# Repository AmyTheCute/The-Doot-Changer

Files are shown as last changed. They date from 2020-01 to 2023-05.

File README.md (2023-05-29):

# The-Doot-Changer

**Warning, project is abandonded for the time being, potential Doot Eternal might be in progress down the line, for the time being, feel free to email me at Amythemaplebun@gmail.com to ask for guidance/files to fit this project into your own printers, or simply ask for what I learned making this tool changer**

Files and designs for The Doot Changer
Welcome to the official page for the Doot Changer Project! Keep in mind that Doot Changer Twist is still in alpha and although this version is working well you should build it at risk

Update: this project is seriously out of date.
But I'm planning on leaving the country for education. I'm designing a far superior version. expect fast printing speeds, a more awesome mechanism when i finally arrive!
However, aside from the motion system you should feel free to transfer the locking mechanism to your printer, however if you're in a hurry you can Message me to design you the new locking mechanism, or you can simply upgrade when i'm done as it barely costs anything to upgreade (it needs aluminium tape and yup, that's it. add 2 wires to your carriage and leave it there for the upgrade

**WARNING**: Doot Changer Twist is missing some files. Contact me at Twitter: https://twitter.com/AmyTheBun to get the files, they're unoptimized and therefore not published. They'll be re-designed and published very soon

Doot Changer Mag Is well tested with bowden tools.

The Doot Changer project is aiming to bring tool changing to the average hobbyists to encourage creative tool design and so on. The Doot Changer Mag is well tested with bowden tools and slightly tested with directdrive tools.

Doot Changer Mag barely costs 20$ in BOM and can be added very easily to any existing printer that moves the hotend in both the X and Y axis. the assembly is very easily and the Y Axis space reducion is dependant on the printer. Expect 50-100mm of y axis loss.
Doot Changer Mag is also self aligning and generally more trouble free, upon crashes the tool is more likely to just fall and if the docks aren't aligned it'll pick itself up. Subtractive tools aren't tested yet. Only bowden tools are tested extensively and directdrive tools are only simulated by attaching weights to the bowden tools (300g) at 1200 accel
The Doot Changer Mag motion system is HIGHLY RECOMMENDED if you're using a HEVO for a faster printing speed and higher print quality. Currently you'd need to design your Own cariage to make it work with Mag but it should be very easy.

Doot Changer Twist is an entire 3DPrinter that costs 600-800$ depending on your config with 2 tools. the "Sweet spot" config costs 750$ on aliexpress with 2 trianglelab BMG + V6 tools, Robodigg Rails and a tooling plate + a 220v AC heated bed.
Doot Changer Twist uses a Motor (Right now, 28-BYJ-48, Soon it'll switch to a no-name toy DC motor) to lock the tools. therefore to unlock the tools you'd have to break the plastic components. This tool changer changer is far less forgiving to mistakes but has a stronger lock.
The docks for this tool changer also take less space but there are more compact docks potentially in work for the Doot Changer Mag. This printer mainly uses dowel pins and you can use Acetal filament for the wedge.
This printer is also a 150$ upgraede (1 additional trinaglelab tools with extruders) for any existing HEVO and reduces anywhere from 80-100mm of Y Axis usable print volume due to the tools taking space. if building a Doot Changer from scratch simply increase the Y axis by 100-110mm and the x axis by 10-20mm (to make space for potential endstop auto nozzle calibrations and accessories) The rods should remain the same size as well as the X axis rails, However a rod holder will need to be designed (ask me for help!)

This project took a year and made my skin bleed, took all my time and cost me more than 1500$ of prototype and researching. I put my heart into this project and chose to use easily sourcable materials so everyone can enjoy what I enjoy.
Please consider donating to this open source project with Crypto Currency or gift cards, I live in Iran so there are no other options for donations sadly. I'm HOPEFULLY moving to canada by next year. I plan to design a far better printer there if I get free time!
Do message me if you decide to donate so I can squeak out loud very hard ;3 (never made a penny before!)

Update!: Thanks to awesome Anya (https://twitter.com/_Iyalei?s=09) for being the first doot changer donator ^~^ bunny heart is truly molten and warm enough to print PEEK

ToDo: Youtube guide

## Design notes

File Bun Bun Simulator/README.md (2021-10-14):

This is a per tool pebble wiper that has the BOM fo only a spring

EDIT: WARNING! this design stopped working, no idea why but the pebbles stick so hard to the kapton tape now that even with my nails it takes a lot of effort to push it, so it needs powerful springs (3x the same spring I use, which is troublesome because my fan duct is what's pushing it and it's not very strongly mounted)

i'm working on 4 new designs that hopefully might work, so in the meantime, try this at your own risk! tho i gotta admit abs works perfect with this, but PLA specially sticks SUPER well, to the point of it not being able to be poked off without help. and the slope at the end of the block sometimes makes the not fully cooled filament deform and get under the block's rail, anyways I have a few ideas on how to fix it! but i'm very sick

If you plan on modifying this to fit another printer, know that some tilt/flex is a good thing if you plant to use the wiping moving block (Block.stl) as a brush to hit the tip of the nozzle too as it has chamfers to rub on the nozzles and some flex helps. however this isn't necessary and you can always add a silicone brush at the end

The extension spring I used:
Length without hooks: 25mm
inside diameter: 5mm
Material: carbon steel?
Image:

That's all I could find, you could also find something slightly weaker and  put it on both sides to insure that the pellets won't hit the spring? I haven't had issues so far tho.
the springs need to stretch 13-14mm and be left a bit stretched still in their "relaxed" poisition. so in total they need 15-18mm~ of travel

To assemble, Put lubrication compatible with your Block.stl (expect for any Nylon/acetal which doesn't need it) on all faces the block moves on expect the top one.
Put Kapton tape on where the pebble will be purged with some aluminium foil/tape under.
Put aluminium foil where the pellet/nozzle would touch to reduce the chance of adhesion.

here's mine:



Here's an older version in action!:
https://twitter.com/AmyTheBun/status/1445347870236946432?s=20

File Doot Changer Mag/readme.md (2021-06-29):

This is the Github page for The Doot Changer

Here are some footage and images and videos:
https://photos.app.goo.gl/33gT6J51nGpFnPVe7

This is printer mostly a modified HEVO but the actual tool changer is super modular and works with anything that moves the toolhead in both X and Y. A ton of credit goes to scott3d tech2c and other people I mentioned in the thingiverse page! Thank you all lovely people!

It's based of my HEVO. The stock build is MOSTLY for bowden but will work for direct drives potentially (limited testing). to make it work with dremels or heavier tools use the small circular hole for an additional magnet (it's only an indicator of where to put it, make it larger and use a ring magnet. keep in mind that if you want to add this YOU MUST NOT LET THE TWO MIDDLE MAGNETS TOUCH each other, put atleast 0.2mm or more space between the two, don't make it way too far tho. Magnets lose strengh quickly when too far apart)

my doot changer 2.0 is in the works, it's going well. I probably will at least ad the motion system as an addon here, it's much better than the stock one. plus it frees up the space lost to the docks

feel free to message me at https://twitter.com/AmyTheBun to ask anything

Donations (bitcoin only cause I live in Iran :( ):

Bitcoin wallet: bc1qhk2vj8rvw50vd60455dnn2gya4cqduanyrnwg3

for lightning network donations contact me at amythechloe@gmail.com since the links expire

XRP (Ripple): rGJVbxGnUKjaEziDkd7TMDE6gjxK1qMbLc

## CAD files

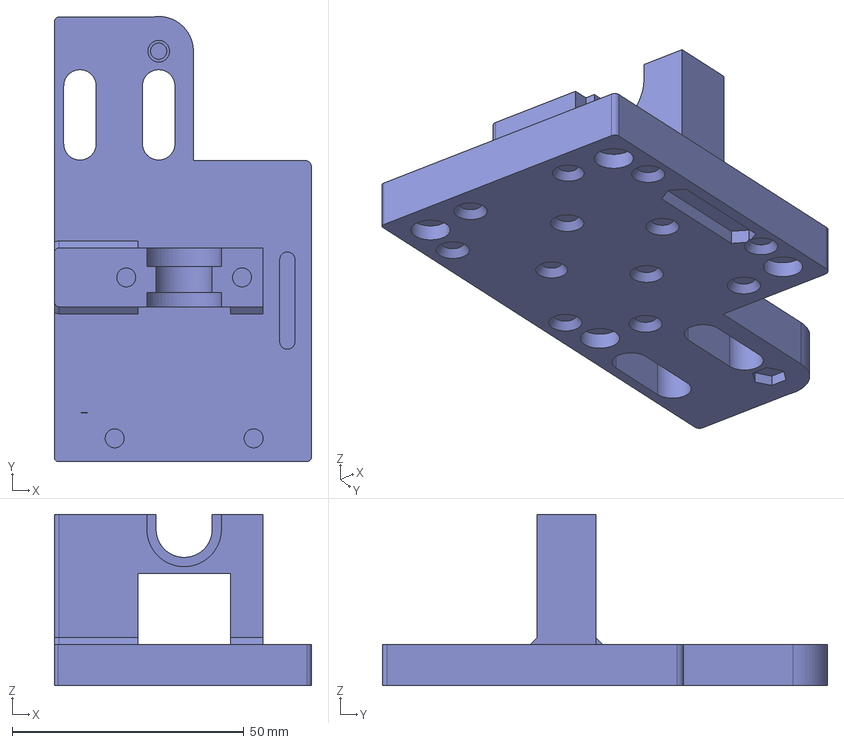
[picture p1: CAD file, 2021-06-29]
Doot Changer Mag/Carriage/Hotend assembly Tool Changer Included.iges
55.5 x 96.1 x 37.0 mm

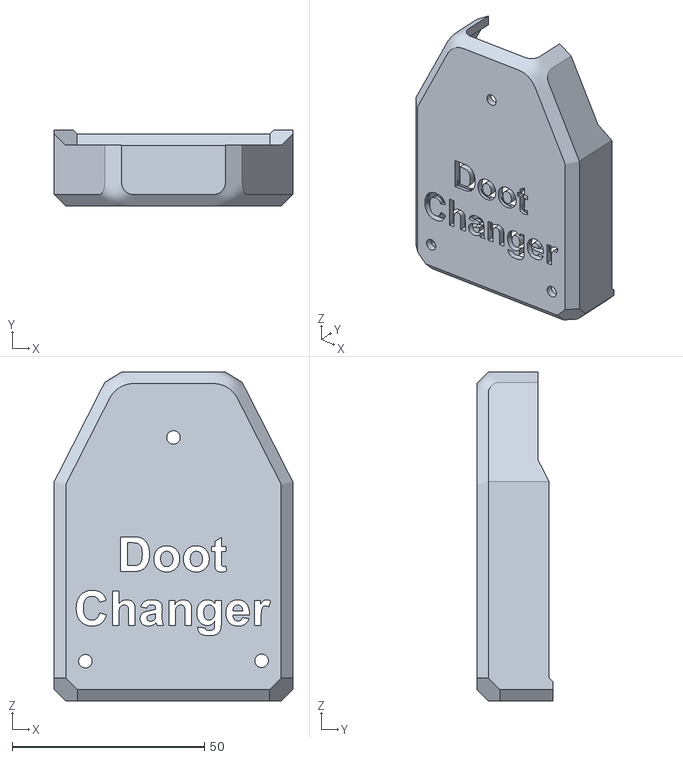
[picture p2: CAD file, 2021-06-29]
Doot Changer Twist/STL/Doot Changing Reward/Main.stl
62.0 x 19.8 x 85.5

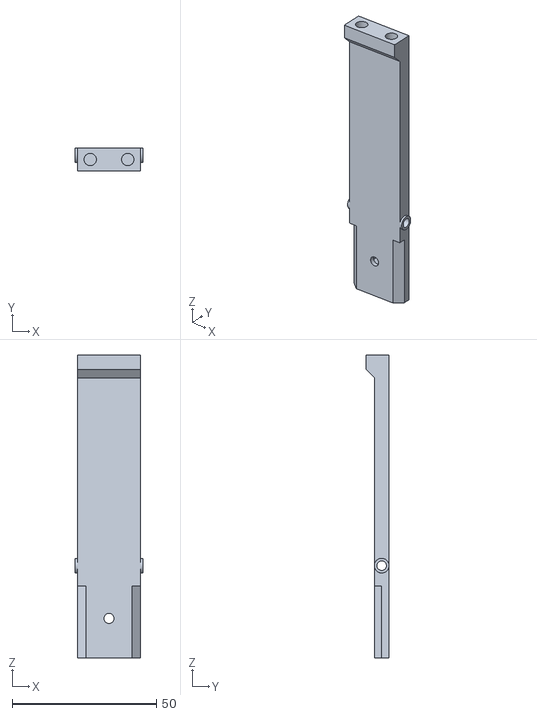
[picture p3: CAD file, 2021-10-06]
Bun Bun Simulator/Arm_Main.stl
23.6 x 8.00 x 105.0

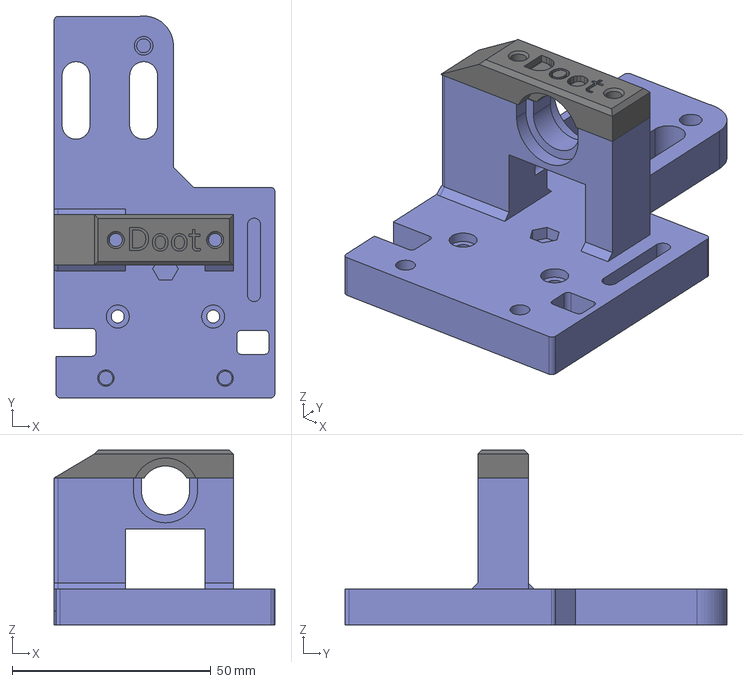
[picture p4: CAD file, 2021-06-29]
Doot Changer Mag/Carriage/Hotend assembly v10.iges
55.5 x 96.1 x 44.0 mm

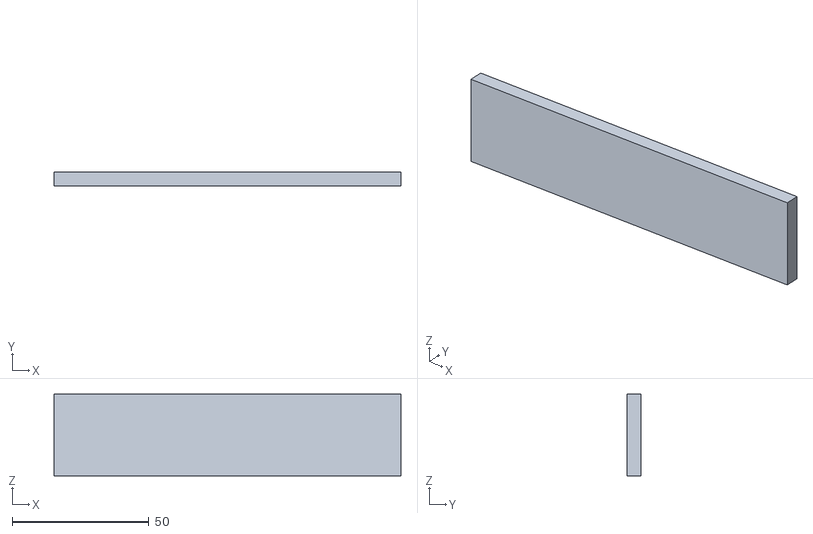
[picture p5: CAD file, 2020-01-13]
Doot Changer Mag/Logo/main.stl
127.0 x 5.00 x 30.0

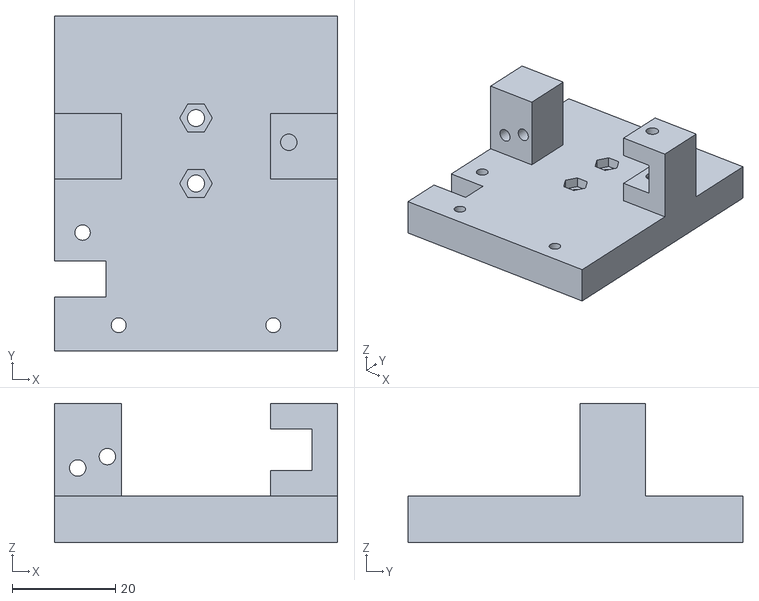
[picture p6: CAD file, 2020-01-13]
Doot Changer Mag/Depricated/Nozzle probe/actually main caswe.stl
55.0 x 65.0 x 27.0

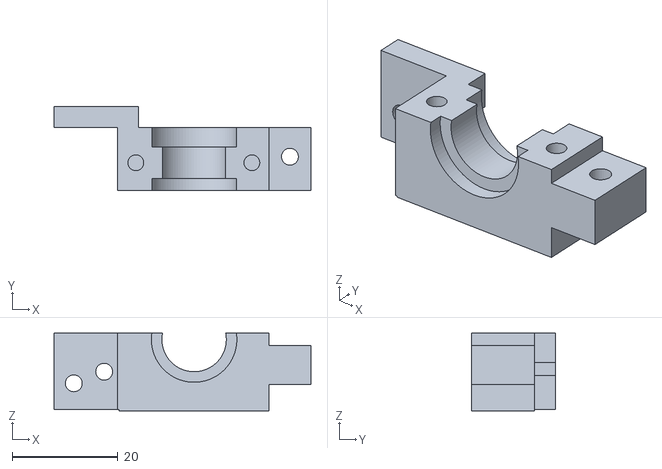
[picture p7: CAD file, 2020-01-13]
Doot Changer Mag/Depricated/Nozzle probe/main case.stl
48.7 x 16.0 x 14.7

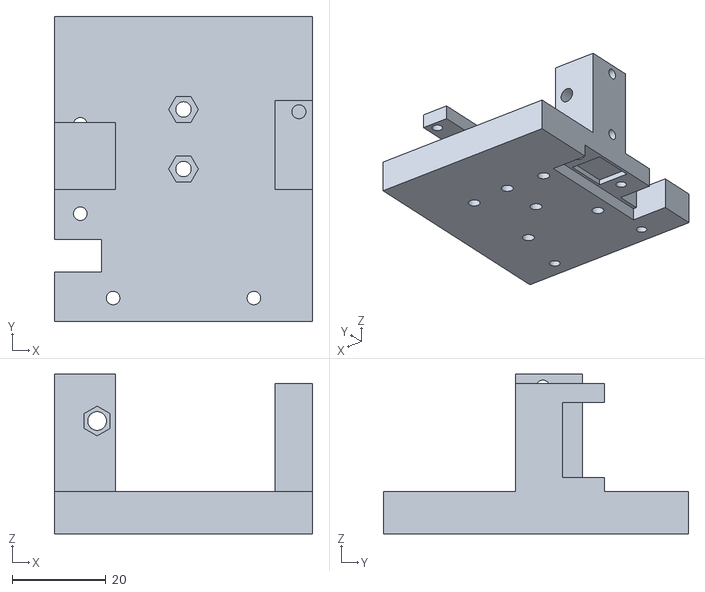
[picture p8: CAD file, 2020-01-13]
Doot Changer Mag/Depricated/Nozzle probe/hotend assembly.stl
55.0 x 65.0 x 34.0

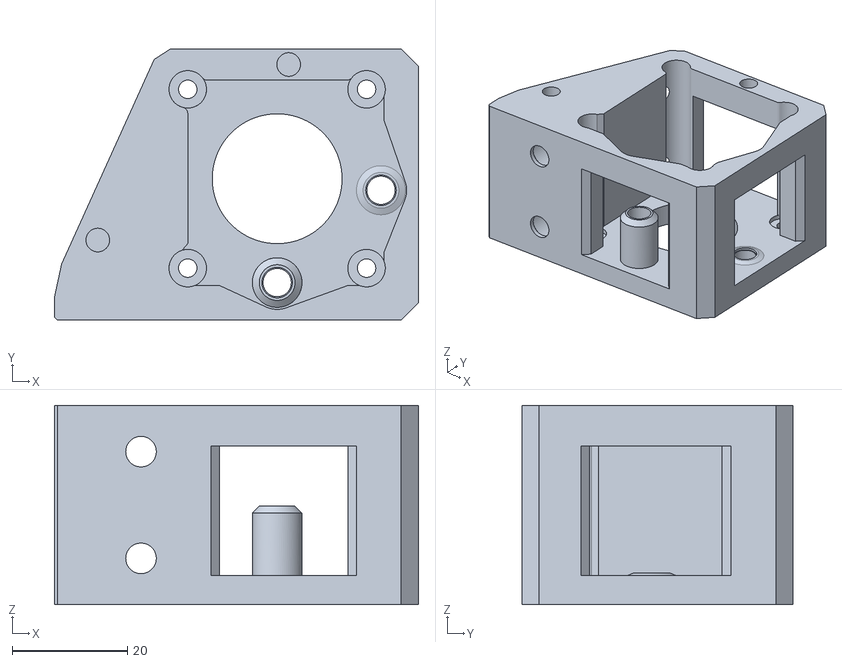
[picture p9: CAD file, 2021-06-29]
Doot Changer Twist/STL/Left_Motor_Main.stl
63.1 x 47.0 x 34.5

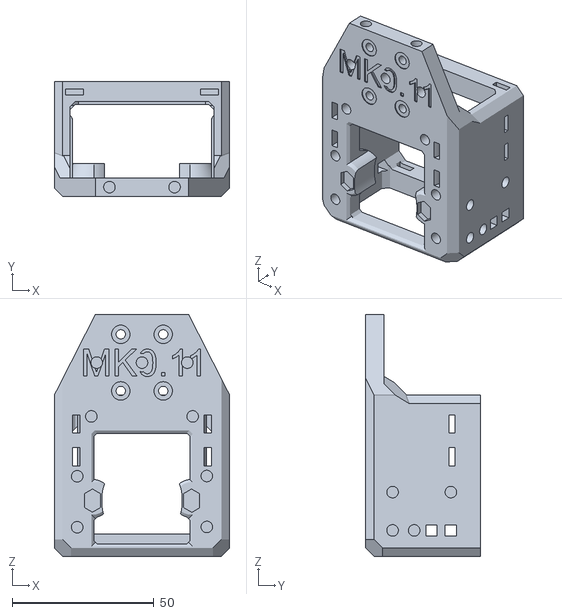
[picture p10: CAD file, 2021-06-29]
Doot Changer Twist/STL/Carriage_Main.stl
62.0 x 40.5 x 85.5

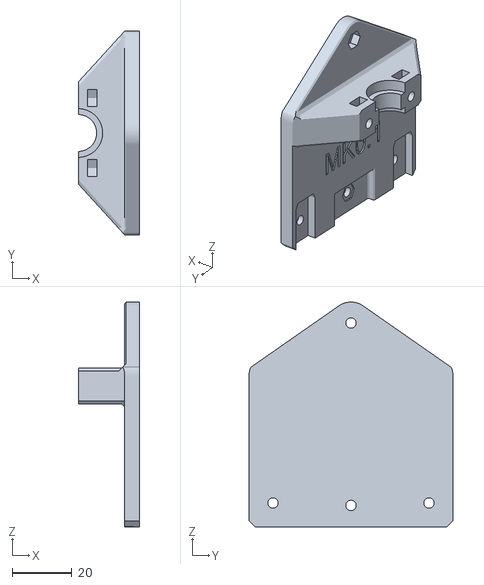
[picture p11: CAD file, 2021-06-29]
Doot Changer Twist/STL/Hotend_Tool_Main.stl
20.5 x 68.0 x 75.0

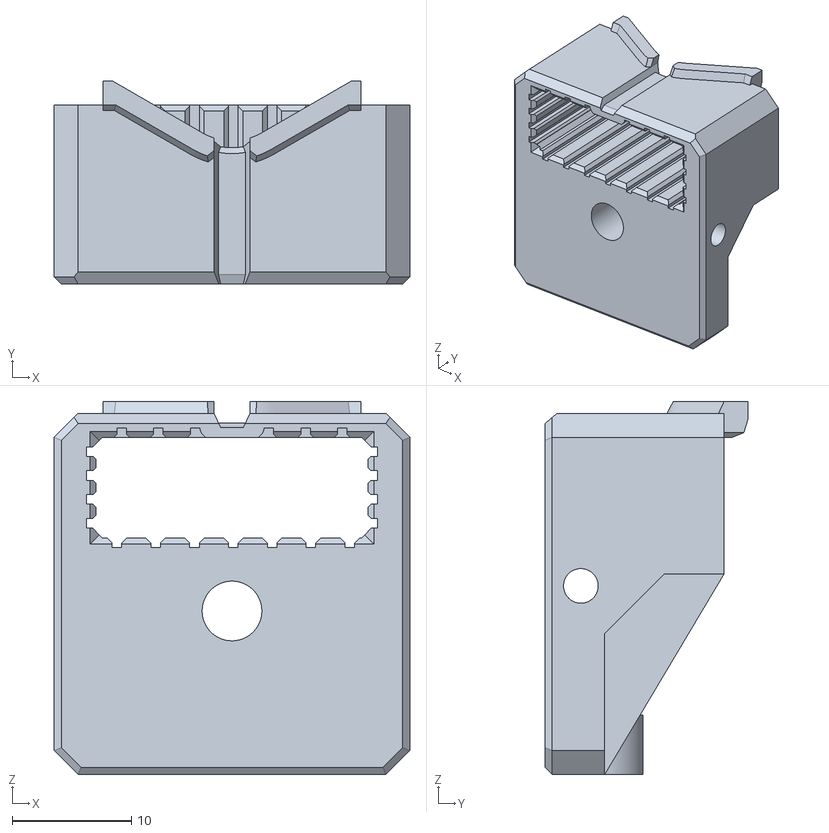
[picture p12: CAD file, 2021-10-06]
Bun Bun Simulator/Block.stl
29.8 x 17.0 x 31.3

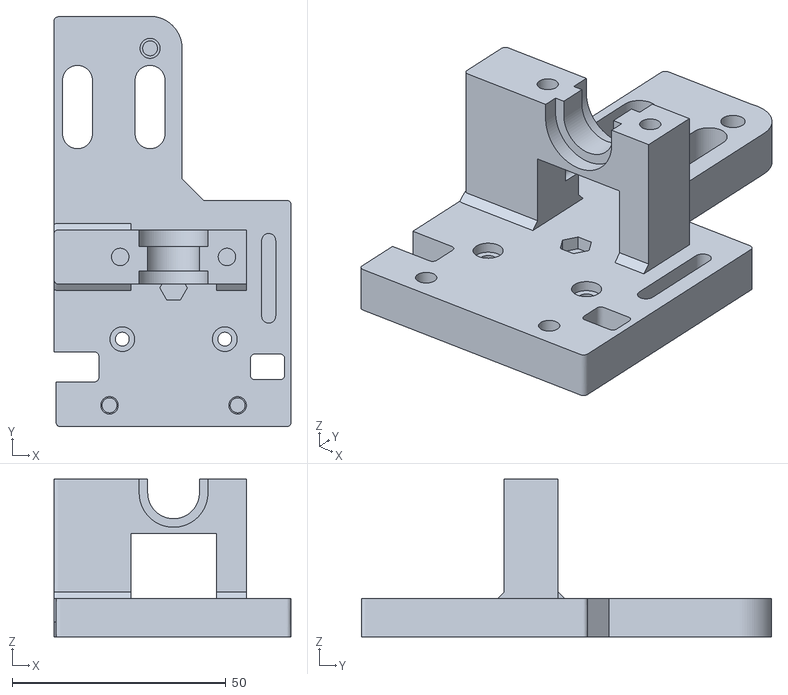
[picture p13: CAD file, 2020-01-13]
Carriage/Hotend_Mount.stl
55.5 x 96.1 x 37.0

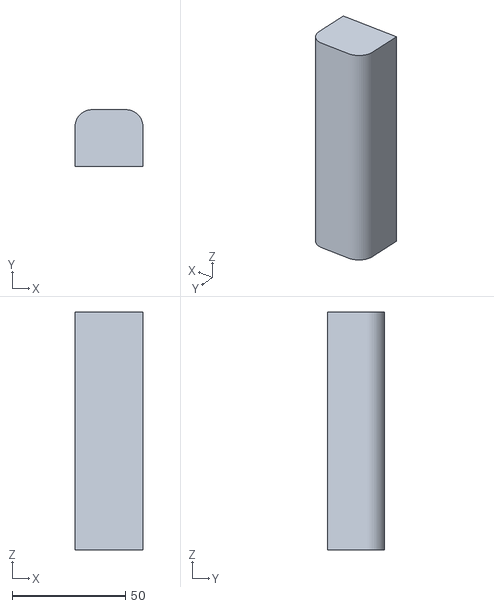
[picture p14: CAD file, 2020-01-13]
Doot Changer Mag/Assembly Tools/Y Axis Extrusion Spacers.stl
30.0 x 25.0 x 105.0

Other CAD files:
Doot Changer Twist/STL/Right_Motor_Main.stl
Doot Changer Mag/Cable Managment/Split Loom Holder v1.stl
Doot Changer Mag/Carriage/Tool Changer/Dock.stl
Doot Changer Mag/Depricated/Doot changer/magnets as doot 1.stl
Bun Bun Simulator/Arm(x2).stl
Bun Bun Simulator/Bottom.stl
Bun Bun Simulator/CAD/Bun Bun Simulator v13.f3d
Bun Bun Simulator/Lever.stl
Doot Changer Mag/Carriage/Hotend_Mount_Clamp.stl
Doot Changer Mag/Carriage/Tool Changer/Carriage plate_V2.stl
Doot Changer Mag/Carriage/Tool Changer/Dock Improved V1.5.iges
Doot Changer Mag/Carriage/Tool Changer/Dock.f3d
Doot Changer Mag/Carriage/Tool Changer/Dock_Mirrored.stl
Doot Changer Mag/Carriage/Tool Changer/Drool_Catchy_V6.stl
Doot Changer Mag/Carriage/Tool Changer/Drool_Catchy_Volcano.stl
Doot Changer Mag/Carriage/Tool Changer/Tool Changer 2 v3.iges
Doot Changer Mag/Carriage/Tool Changer/Tool Changer V2.0 v3.f3d
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

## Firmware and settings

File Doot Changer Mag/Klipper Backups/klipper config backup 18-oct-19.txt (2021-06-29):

# This file serves as documentation for config parameters. One may
# copy and edit this file to configure a new cartesian style
# printer. For delta style printers, see the "example-delta.cfg"
# file. For corexy/h-bot style printers, see the "example-corexy.cfg"
# file. Only common config sections are described here - see the
# "example-extras.cfg" file for configuring less common devices.

# DO NOT COPY THIS FILE WITHOUT CAREFULLY READING AND UPDATING IT
# FIRST. Incorrectly configured parameters may cause damage.

# A note on pin names: pins may be configured with a hardware name
# (such as "PA4") or with an Arduino alias name (such as "ar29" or
# "analog3"). In order to use Arduino names, the pin_map variable in
# the mcu section must be present and have a value of "arduino". Pin
# names may be preceded by an '!' to indicate that a reverse polarity
# should be used (eg, trigger on low instead of high). Input pins may
# be preceded by a '^' to indicate that a hardware pull-up resistor
# should be enabled for the pin. If the micro-controller supports
# pull-down resistors then an input pin may alternatively be preceded
# by a '~'.


# The stepper_x section is used to describe the stepper controlling
# the X axis in a cartesian robot.
[stepper_x]
step_pin: ar54
#   Step GPIO pin (triggered high). This parameter must be provided.
dir_pin: ar55
#   Direction GPIO pin (high indicates positive direction). This
#   parameter must be provided.
enable_pin: !ar38
#   Enable pin (default is enable high; use ! to indicate enable
#   low). Alternatively, this may be a comma separated list of pins to
#   enable. If this parameter is not provided then the stepper motor
#   driver must always be enabled.
step_distance: .0125
#   Distance in mm that each step causes the axis to travel. This
#   parameter must be provided.
endstop_pin: ^ar3
#   Endstop switch detection pin. This parameter must be provided for
#   the X, Y, and Z steppers on cartesian style printers.
#position_min: 0
#   Minimum valid distance (in mm) the user may command the stepper to
#   move to.  The default is 0mm.
position_endstop: 0
#   Location of the endstop (in mm). This parameter must be provided
#   for the X, Y, and Z steppers on cartesian style printers.
position_max: 300
homing_speed: 40.0
#homing_retract_dist: 5.0
#second_homing_speed:
#homing_positive_dir:


[stepper_y]
step_pin: ar60
dir_pin: ar61
enable_pin: !ar56
step_distance: .0125
endstop_pin: ^ar14
homing_speed: 40.0
position_endstop: 0
position_max: 300

[stepper_z]
step_pin: ar46
dir_pin: ar48
enable_pin: !ar62
step_distance: .0025
#endstop_pin: ^ar18
#position_endstop: 0
endstop_pin: probe:z_virtual_endstop
position_max: 285
position_min: -5
homing_speed: 10

[extruder]
step_pin: ar26
dir_pin: ar28
enable_pin: !ar24
step_distance: 0.0022917632352941
nozzle_diameter: 0.4
filament_diameter: 1.7500
#max_extrude_cross_section:
max_extrude_only_distance: 650
#max_extrude_only_velocity:
#max_extrude_only_accel:
pressure_advance: 0.31
#pressure_advance_lookahead_time: 0.010
heater_pin: ar10
#max_power: 1.0
sensor_type: ATC Semitec 104GT-2
#   Type of sensor - this may be "EPCOS 100K B57560G104F", "ATC
#   Semitec 104GT-2", "NTC 100K beta 3950", "Honeywell 100K
#   135-104LAG-J01", "NTC 100K MGB18-104F39050L32", "AD595", "PT100
#   INA826", "MAX6675", "MAX31855", "MAX31856", or "MAX31865".
#   Additional sensor types may be available - see the
#   example-extras.cfg file for details. This parameter must be
#   provided.
sensor_pin: analog13
#pullup_resistor: 4700
#inline_resistor: 0
#adc_voltage: 5.0
#smooth_time: 2.0
#control: pid
#pid_Kp: 16.34
#pid_Ki: 1.16
#pid_Kd: 57.57
#pid_integral_max:
#pwm_cycle_time: 0.100
#   Time in seconds for each software PWM cycle of the heater. It is
#   not recommended to set this unless there is an electrical
#   requirement to switch the heater faster than 10 times a second.
#   The default is 0.100 seconds.
#min_extrude_temp: 170
#   The minimum temperature (in Celsius) at which extruder move
#   commands may be issued. The default is 170 Celsius.
min_temp: 0
max_temp: 260
#   The maximum range of valid temperatures (in Celsius) that the
#   heater must remain within. This controls a safety feature
#   implemented in the micro-controller code - should the measured
#   temperature ever fall outside this range then the micro-controller
#   will go into a shutdown state. This check can help detect some
#   heater and sensor hardware failures. Set this range just wide
#   enough so that reasonable temperatures do not result in an
#   error. These parameters must be provided.

[extruder1]
step_pin: ar36
dir_pin: !ar34
enable_pin: !ar30
#step_distance: .0.0025364567057292
nozzle_diameter: 0.4
filament_diameter: 1.7500
max_extrude_only_distance: 650
pressure_advance: 0.31
shared_heater: extruder

# The heater_bed section describes a heated bed (if present - omit
# section if not present).
[heater_bed]
heater_pin: ar45
sensor_type: NTC 100K beta 3950
sensor_pin: analog14
control: pid
pid_Kp: 54.73
pid_Ki: 1.69
pid_Kd: 1180.74
#max_delta: 2.0
#   On 'watermark' controlled heaters this is the number of degrees in
#   Celsius above the target temperature before disabling the heater
#   as well as the number of degrees below the target before
#   re-enabling the heater. The default is 2 degrees Celsius.
min_temp: 0
max_temp: 110
max_power: 0.8

# Print cooling fan 
[fan]
pin: ar44
#max_power: 1.0
#shutdown_speed: 0
#   The desired fan speed (expressed as a value from 0.0 to 1.0) if
#   the micro-controller software enters an error state. The default
#   is 0.
#cycle_time: 0.010
#   The amount of time (in seconds) for each PWM power cycle to the
#   fan. It is recommended this be 10 milliseconds or greater when
#   using software based PWM. The default is 0.010 seconds.
#hardware_pwm: False
#   Enable this to use hardware PWM instead of software PWM. Most fans
#   do not work well with hardware PWM, so it is not recommended to
#   enable this unless there is an electrical requirement to switch at
#   very high speeds. When using hardware PWM the actual cycle time is
#   constrained by the implementation and may be significantly
#   different than the requested cycle_time. The default is False.
#kick_start_time: 0.100
#   Time (in seconds) to run the fan at full speed when first enabling
#   it (helps get the fan spinning). The default is 0.100 seconds.

# Micro-controller information.
[mcu]
serial: /dev/ttyUSB0
#   The serial port to connect to the MCU. If unsure (or if it
#   changes) see the "Where's my serial port?" section of the FAQ. The
#   default is /dev/ttyS0
#baud: 250000
#   The baud rate to use. The default is 250000.
pin_map: arduino
#   This option may be used to enable Arduino pin name aliases. The
#   default is to not enable the aliases.
#restart_method:
#   This controls the mechanism the host will use to reset the
#   micro-controller. The choices are 'arduino', 'rpi_usb', and
#   'command'. The 'arduino' method (toggle DTR) is common on Arduino
#   boards and clones. The 'rpi_usb' method is useful on Raspberry Pi
#   boards with micro-controllers powered over USB - it briefly
#   disables power to all USB ports to accomplish a micro-controller
#   reset. The 'command' method involves sending a Klipper command to
#   the micro-controller so that it can reset itself. The default is
#   'arduino' if the micro-controller communicates over a serial port,
#   'command' otherwise.
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

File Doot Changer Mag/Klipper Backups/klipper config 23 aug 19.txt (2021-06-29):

deb http://raspbian.raspberrypi.org/raspbian/ stretch main contrib non-free rpi
# Uncomment line below then 'apt-get update' to enable 'apt-get source'
#deb-src http://raspbian.raspberrypi.org/raspbian/ stretch main contrib non-free rpi

## Configure a TMC2208 (or TMC2224) stepper motor driver via single
# wire UART. To use this feature, define a config section with a
# "tmc2208" prefix followed by the name of the corresponding stepper
# config section (for example, "[tmc2208 stepper_x]"). This also
# creates a "tmc2208_stepper_x:virtual_enable" virtual pin which may
# be used as the stepper's enable_pin (for enabling the driver via a
# UART message).

[tmc2208 stepper_x]
uart_pin: ar20
#   The pin connected to the TMC2208 PDN_UART line. This parameter
#   must be provided.
#tx_pin: ar20
#   If using separate receive and transmit lines to communicate with
#   the driver then set uart_pin to the receive pin and tx_pin to the
#   transmit pin. The default is to use uart_pin for both reading and
#   writing.
#select_pins:
#   A comma separated list of pins to set prior to accessing the
#   tmc2208 UART. This may be useful for configuring an analog mux for
#   UART communication. The default is to not configure any pins.
microsteps: 16
#   The number of microsteps to configure the driver to use. Valid
#   values are 1, 2, 4, 8, 16, 32, 64, 128, 256. This parameter must
#   be provided.
#interpolate: True
#   If true, enable step interpolation (the driver will internally
#   step at a rate of 256 micro-steps). The default is True.
run_current: 0.81
#   The amount of current (in amps) to configure the driver to use
#   during stepper movement. This parameter must be provided.
hold_current: 0.4
#   The amount of current (in amps) to configure the driver to use
#   when the stepper is not moving. The default is to use the same
#   value as run_current.
#sense_resistor: 0.110
#   The resistance (in ohms) of the motor sense resistor. The default
#   is 0.110 ohms.
#stealthchop_thres hold: 0
#   The velocity (in mm/s) to set the "stealthChop" threshold to. When
#   set, "stealthChop" mode will be enabled if the stepper motor
#   velocity is below this value. The default is 0, which disables
#   "stealthChop" mode.
#driver_IHOLDDELAY: 8
#driver_TPOWERDOWN: 20
#driver_TBL: 2
#driver_TOFF: 3
#driver_HEND: 0
#driver_HSTRT: 5
#driver_PWM_AUTOGRAD: True
#driver_PWM_AUTOSCALE: True
#driver_PWM_LIM: 12
#driver_PWM_REG: 8
#driver_PWM_FREQ: 1
#driver_PWM_GRAD: 14
#driver_PWM_OFS: 36
#   Set the given register during the configuration of the TMC2208
#   chip. This may be used to set custom motor parameters. The
#   defaults for each parameter are next to the parameter name in the
#   above list

[tmc2208 stepper_y]
uart_pin: ar21
#   The pin connected to the TMC2208 PDN_UART line. This parameter
#   must be provided.
#tx_pin: ar21
#   If using separate receive and transmit lines to communicate with
#   the driver then set uart_pin to the receive pin and tx_pin to the
#   transmit pin. The default is to use uart_pin for both reading and
#   writing.
#select_pins:
#   A comma separated list of pins to set prior to accessing the
#   tmc2208 UART. This may be useful for configuring an analog mux for
#   UART communication. The default is to not configure any pins.
microsteps: 16
#   The number of microsteps to configure the driver to use. Valid
#   values are 1, 2, 4, 8, 16, 32, 64, 128, 256. This parameter must
#   be provided.
#interpolate: True
#   If true, enable step interpolation (the driver will internally
#   step at a rate of 256 micro-steps). The default is True.
run_current: 0.81
#   The amount of current (in amps) to configure the driver to use
#   during stepper movement. This parameter must be provided.
hold_current: 0.4
#   The amount of current (in amps) to configure the driver to use
#   when the stepper is not moving. The default is to use the same
#   value as run_current.
#sense_resistor: 0.110
#   The resistance (in ohms) of the motor sense resistor. The default
#   is 0.110 ohms.
#stealthchop_thres hold: 0
#   The velocity (in mm/s) to set the "stealthChop" threshold to. When
#   set, "stealthChop" mode will be enabled if the stepper motor
#   velocity is below this value. The default is 0, which disables
#   "stealthChop" mode.
#driver_IHOLDDELAY: 8
#driver_TPOWERDOWN: 20
#driver_TBL: 2
#driver_TOFF: 3
#driver_HEND: 0
#driver_HSTRT: 5
#driver_PWM_AUTOGRAD: True
#driver_PWM_AUTOSCALE: True
#driver_PWM_LIM: 12
#driver_PWM_REG: 8
#driver_PWM_FREQ: 1
#driver_PWM_GRAD: 14
#driver_PWM_OFS: 36
#   Set the given register during the configuration of the TMC2208
#   chip. This may be used to set custom motor parameters. The
#   defaults for each parameter are next to the parameter name in the
#   above list

[tmc2208 stepper_z]
uart_pin: ar4
#   The pin connected to the TMC2208 PDN_UART line. This parameter
#   must be provided.
#tx_pin: ar4
#   If using separate receive and transmit lines to communicate with
#   the driver then set uart_pin to the receive pin and tx_pin to the
#   transmit pin. The default is to use uart_pin for both reading and
#   writing.
#select_pins:
#   A comma separated list of pins to set prior to accessing the
#   tmc2208 UART. This may be useful for configuring an analog mux for
#   UART communication. The default is to not configure any pins.
microsteps: 16
#   The number of microsteps to configure the driver to use. Valid
#   values are 1, 2, 4, 8, 16, 32, 64, 128, 256. This parameter must
#   be provided.
#interpolate: True
#   If true, enable step interpolation (the driver will internally
#   step at a rate of 256 micro-steps). The default is True.
run_current: 0.81
#   The amount of current (in amps) to configure the driver to use
#   during stepper movement. This parameter must be provided.
hold_current: 0.4
#   The amount of current (in amps) to configure the driver to use
#   when the stepper is not moving. The default is to use the same
#   value as run_current.
#sense_resistor: 0.110
#   The resistance (in ohms) of the motor sense resistor. The default
#   is 0.110 ohms.
#stealthchop_thres hold: 0
#   The velocity (in mm/s) to set the "stealthChop" threshold to. When
#   set, "stealthChop" mode will be enabled if the stepper motor
#   velocity is below this value. The default is 0, which disables
#   "stealthChop" mode.
#driver_IHOLDDELAY: 8
#driver_TPOWERDOWN: 20
#driver_TBL: 2
#driver_TOFF: 3
#driver_HEND: 0
#driver_HSTRT: 5
#driver_PWM_AUTOGRAD: True
#driver_PWM_AUTOSCALE: True
#driver_PWM_LIM: 12
#driver_PWM_REG: 8
#driver_PWM_FREQ: 1
#driver_PWM_GRAD: 14
#driver_PWM_OFS: 36
#   Set the given register during the configuration of the TMC2208
#   chip. This may be used to set custom motor parameters. The
#   defaults for each parameter are next to the parameter name in the
#   above list



##PID parameters: pid_Kp=61.000 pid_Ki=1.660 pid_Kd=560.440 bed
Recv: // PID parameters: pid_Kp=15.590 pid_Ki=0.520 pid_Kd=116.926 hotend

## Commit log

2020-01-15 Less tolerance by default to avoid magnets touching
    [Hotend_ToolChanger_Adapter.stl, Tool Changer 2 v3.iges]
2020-03-22 more stable mounting points for the drool catchy's wipe boi
    [Dock Improved V1.5.iges, Drool_Catchy_V6.stl, Drool_Catchy_V6_Mirrored.stl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]
2020-03-23 Extended drool catchy
    [Dock Improved V1.5.iges, Drool_Catchy_V6.stl, Drool_Catchy_Volcano.stl]
2020-04-19 Improved Block ToolPlate
    [Body1.stl, Component4.stl, Tool Changer V2.0 v3.f3d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]
2021-06-29 Doot Changer Mag partially added.
    Doot Changer Mag partial eddition
    [Acetal_Wedge.f3d, Acetal_Wedge.stl, Body1.stl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]
2021-07-23 Better Wedge, Better dock, Stronger carriage cable holder
    [Acetal_Wedge.f3d, Acetal_Wedge.stl, Cable_Loom_Guide.stl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]
2021-10-06 Some updates,
    [Body1.stl, Body2.stl, Carriage_front.stl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]
2021-10-06 Added Bun Bun Simulator
    (still need to push new twist updates tho)
    [Arm(x2).stl, Arm_Main.stl, Block.stl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]
